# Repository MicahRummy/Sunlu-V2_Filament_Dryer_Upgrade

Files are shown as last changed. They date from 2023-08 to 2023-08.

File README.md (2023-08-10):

# Sunlu-V2_Filament_Dryer_Upgrade
 Upgraded the Sunlu PCB and Firmware.

I had to redesign the cover on the orginal design, and cut a hole for the inductor and aliminum capacitor which didn't fit in the original enclosure. I used the wrong JST connectors, so I had to cut a hole for those as well, but that can be avoided with horizontal connectors instead of vertical. I provided all the design files and Code. The PCB, Schematic, and cover were designed inside Fusion 360. I used a generic OLED display, which I got off of amazon, link below. Most other components can be found in the BOD.csv.

UCTRONICS 0.96 Inch OLED Module... https://www.amazon.com/dp/B072Q2X2LL?ref=ppx_pop_mob_ap_share

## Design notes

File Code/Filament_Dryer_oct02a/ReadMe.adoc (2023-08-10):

:Author: micahrumm
:Email:
:Date: 02/10/2022
:Revision: version#
:License: Public Domain

= Project: {Project}

Describe your project

== Step 1: Installation
Please describe the steps to install this project.

For example:

1. Open this file
2. Edit as you like
3. Release to the World!

== Step 2: Assemble the circuit

Assemble the circuit following the diagram layout.png attached to the sketch

== Step 3: Load the code

Upload the code contained in this sketch on to your board

=== Folder structure

....
 sketch123                => Arduino sketch folder
  âââ sketch123.ino       => main Arduino file
  âââ schematics.png      => (optional) an image of the required schematics
  âââ layout.png          => (optional) an image of the layout
  âââ ReadMe.adoc         => this file
....

=== License
This project is released under a {License} License.

=== Contributing
To contribute to this project please contact: 

=== BOM
Add the bill of the materials you need for this project.

|===
| ID | Part name      | Part number | Quantity
| R1 | 10k Resistor   | 1234-abcd   | 10       
| L1 | Red LED        | 2345-asdf   | 5        
| A1 | Arduino Zero   | ABX00066    | 1        
|===

=== Help
This document is written in the _AsciiDoc_ format, a markup language to describe documents. 
If you need help you can search the http://www.methods.co.nz/asciidoc[AsciiDoc homepage]
or consult the http://powerman.name/doc/asciidoc[AsciiDoc cheatsheet]

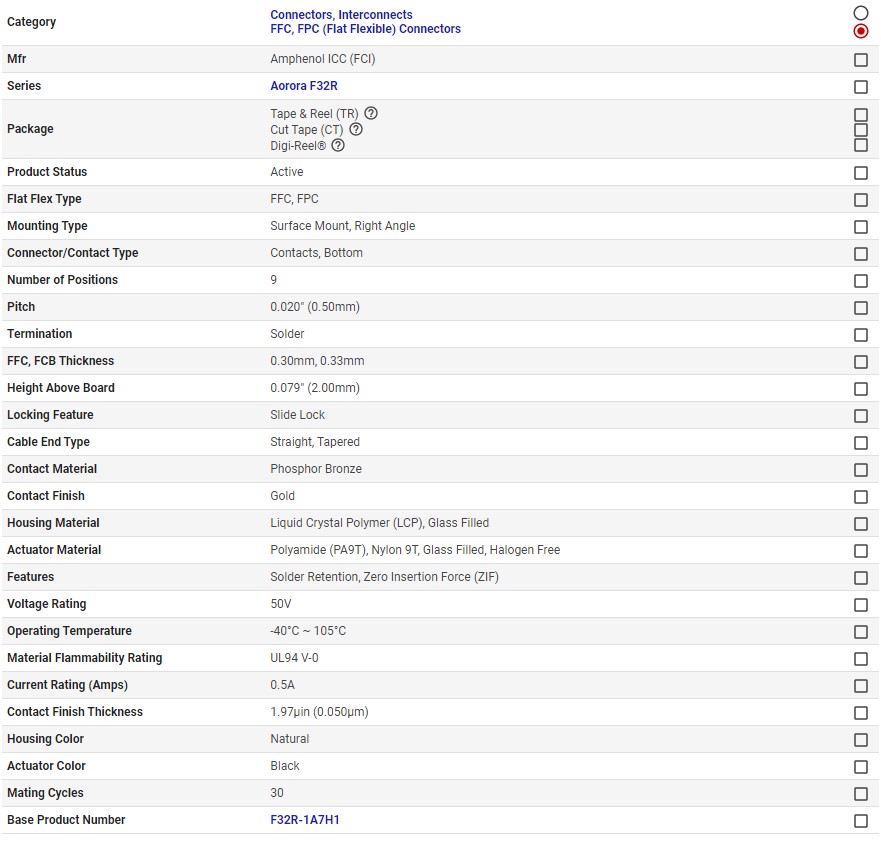
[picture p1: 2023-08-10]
Datasheets/Ribbon Connector Specs_Screenshot 2022-07-01 185358.jpg

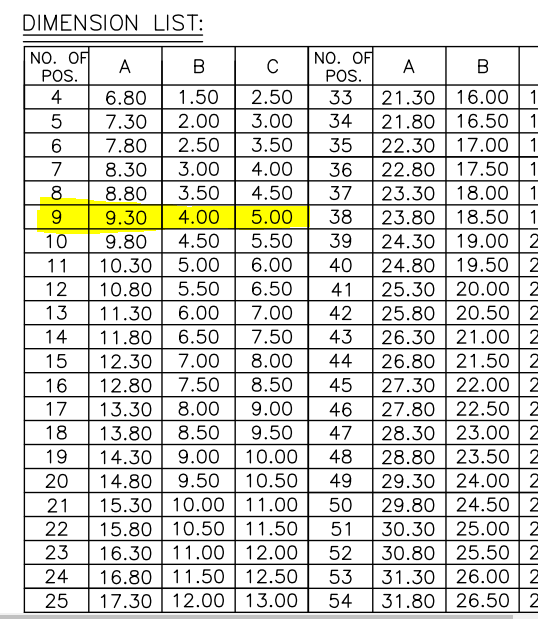
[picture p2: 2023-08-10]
Datasheets/Ribbon Connector.png

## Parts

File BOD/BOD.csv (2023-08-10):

Index | Digi-Key Part # | Manufacturer Part Number | Description | Customer Reference | Quantity | Backorder | Unit Price | Extended Price | Note
1 | 565-4186-1-ND | HHXB350ARA680MF80G | CAP ALUM HYB 68UF 20% 35V SMD |  | 4 | 0 | $1.50 | $6.00
2 | MAX5035BASA+-ND | MAX5035BASA+ | IC REG BUCK 5V 1A 8SOIC |  | 3 | 0 | $5.06 | $15.18
3 | 308-CDRH127L125NP-101MCCT-ND | CDRH127L125NP-101MC | FIXED IND 100UH 2A 171.2MOHM SMD |  | 2 | 0 | $1.40 | $2.80
4 | 3757-SB56AFC_R1_00001CT-ND | SB56AFC_R1_00001 | DIODE SCHOTTKY 60V 5A SMAF-C |  | 4 | 0 | $0.42 | $1.68
5 | 718-1004-1-ND | 594D686X0010C2T | CAP TANT 68UF 20% 10V 2812 |  | 2 | 0 | $3.28 | $6.56
6 | CR0805-FX-1004ELFCT-ND | CR0805-FX-1004ELF | RES SMD 1M OHM 1% 1/8W 0805 |  | 100 | 0 | $0.01 | $1.15
7 | 738-RMCF0805FT383KCT-ND | RMCF0805FT383K | RES 383K OHM 1% 1/8W 0805 |  | 100 | 0 | $0.01 | $1.09
8 | 455-2955-1-ND | BM02B-SRSS-TBT(LF)(SN) | CONN HEADER SMD 2POS 1MM |  | 4 | 0 | $0.64 | $2.56 | Get Horizontal instead of vertical.
9 | 455-2997-ND | A02SR02SR30K51A | JUMPER 02SR-3S - 02SR-3S 2" |  | 2 | 0 | $1.08 | $2.16
10 | WM15692-ND | 797581009 | DURA-CLICK 300MM 26AWG PRE-CRIMP |  | 3 | 0 | $1.33 | $3.99
11 | IRLR2705PBFCT-ND | IRLR2705TRPBF | MOSFET N-CH 55V 28A DPAK | DONT THROW A FET | 10 | 0 | $0.82 | $8.17
12 | 2019-RN73R2ETTD1003B25CT-ND | RN73R2ETTD1003B25 | RESISTOR THIN FILM 1210 SIZE |  | 4 | 0 | $0.80 | $3.20
13 | 1597-113991054-ND | 113991054 | SEEED STUDIO XIAO ESP32C3 WIFI+B |  | 3 | 0 | $4.99 | $14.97
14 | RBR3MM60ATFCT-ND | RBR3MM60ATFTR | DIODE SCHOTTKY 60V 3A PMDU |  | 10 | 0 | $0.32 | $3.17
15 | RMCF0603FT330RCT-ND | RMCF0603FT330R | RES 330 OHM 1% 1/10W 0603 |  | 100 | 0 | $0.01 | $0.61
 |  |  |  |  |  |  | Subtotal | $73.29 | Reuse power connections from old PCB, or find new ones.

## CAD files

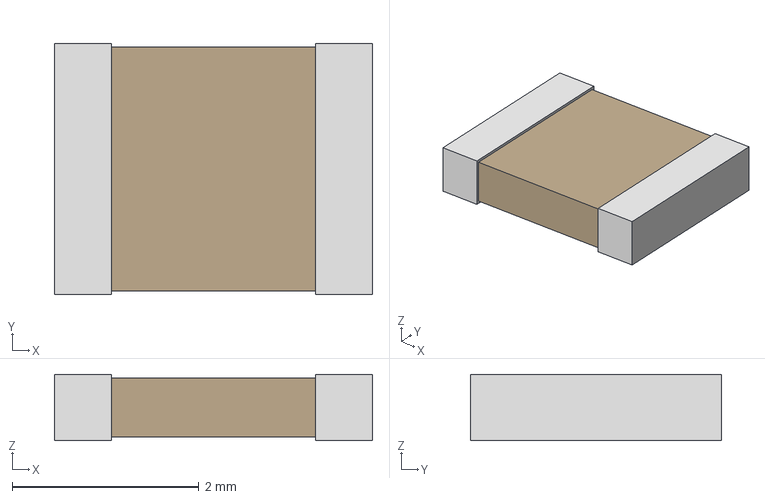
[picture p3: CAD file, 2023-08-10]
Eagle Libraries/100K RESISTOR/ul_RN73R2ETTD1003B25/2022-11-03_19-58-43/STEP/RES_RN73R2E_KOA.step
3.40 x 2.69 x 0.711 mm

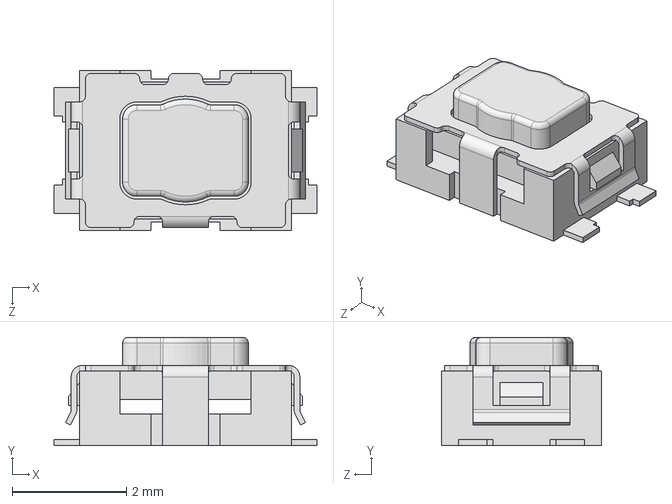
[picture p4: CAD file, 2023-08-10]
Eagle Libraries/Tactile Button/TL6330AF200Q--3DModel-STEP-613395.STEP
4.60 x 1.90 x 2.80 mm

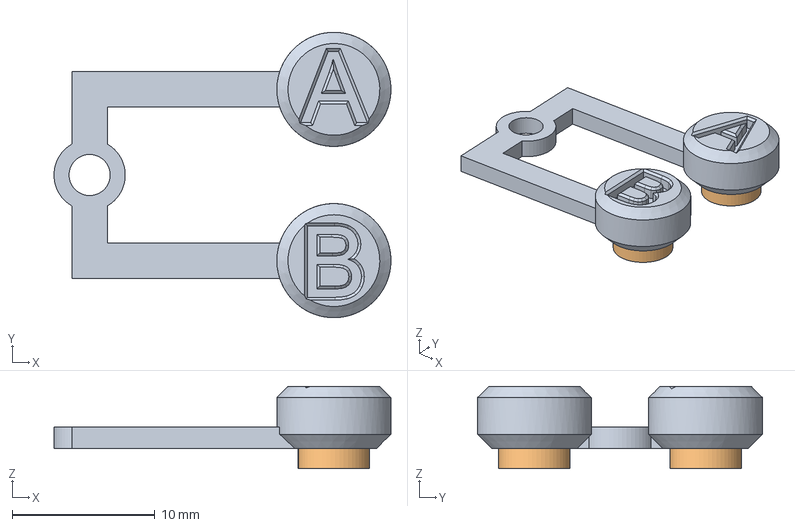
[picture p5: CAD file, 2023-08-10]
Step/Filament Dryer Cover v39.step
23.6 x 20.0 x 5.75 mm

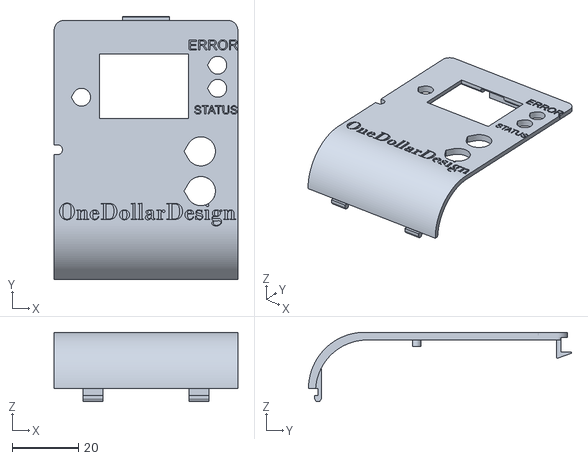
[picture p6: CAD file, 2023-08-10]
stl&3mf/Lid V8.stl
55.5 x 79.5 x 21.0

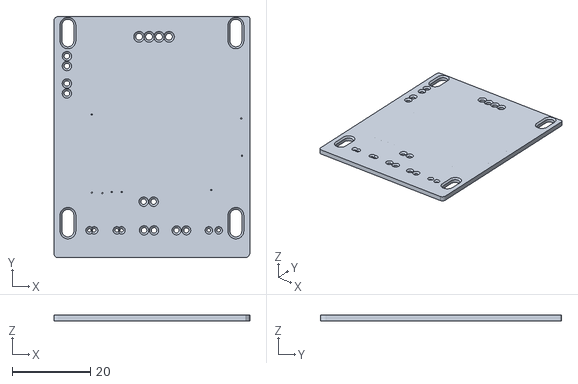
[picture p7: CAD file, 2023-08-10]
stl&3mf/PCB Board 0.2 Tolerance.stl
50.0 x 61.6 x 1.50

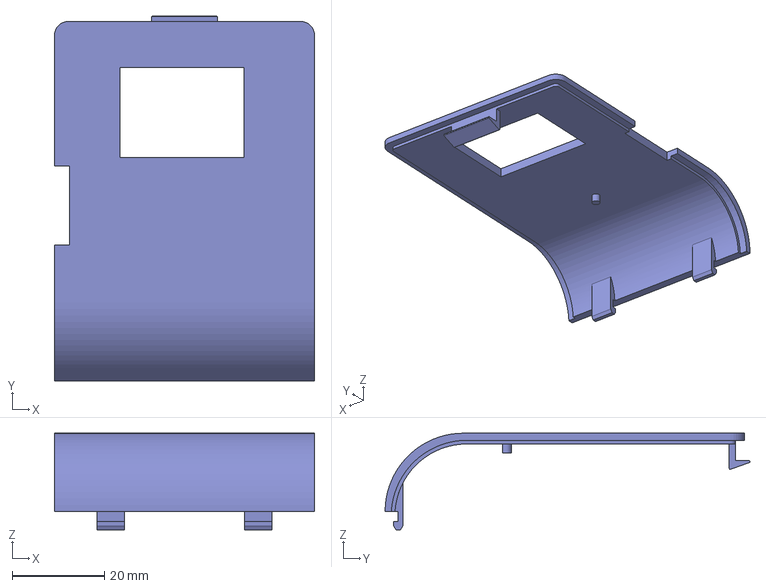
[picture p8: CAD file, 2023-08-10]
stl&3mf/Lid V1.3mf
56.5 x 79.3 x 21.0 mm

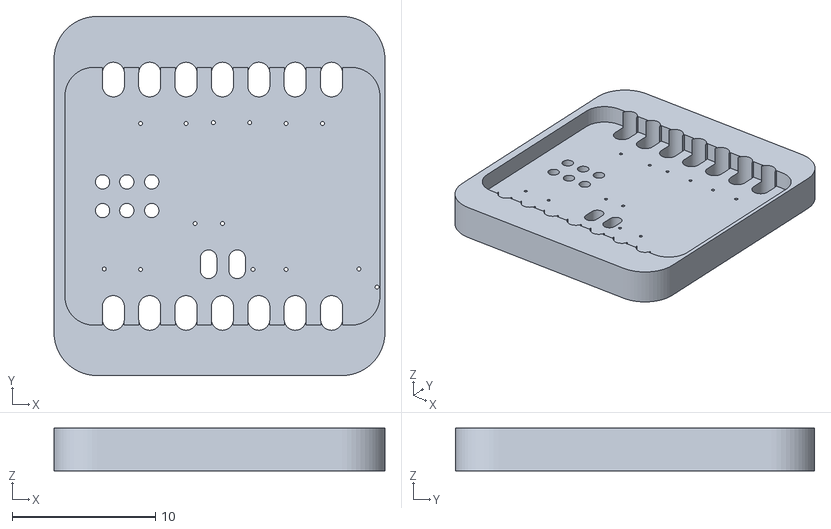
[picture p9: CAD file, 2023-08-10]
stl&3mf/Xiao ESP32 Stencil.stl
23.1 x 25.1 x 3.00

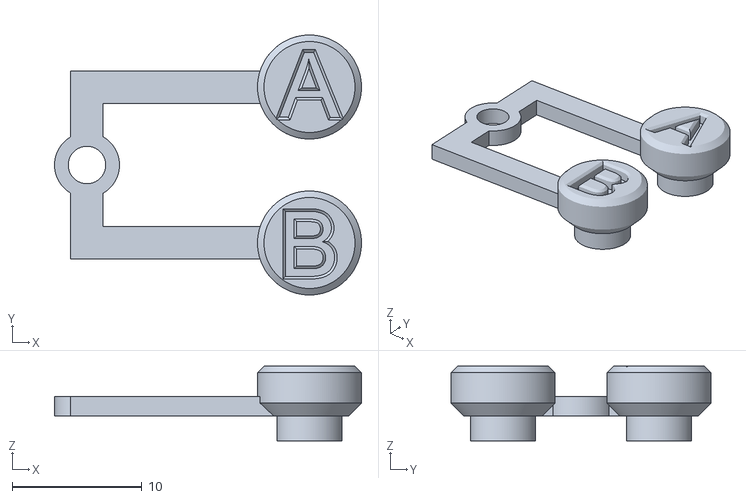
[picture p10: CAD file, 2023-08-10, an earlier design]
stl&3mf/Button Press V4.stl
23.6 x 20.0 x 5.75

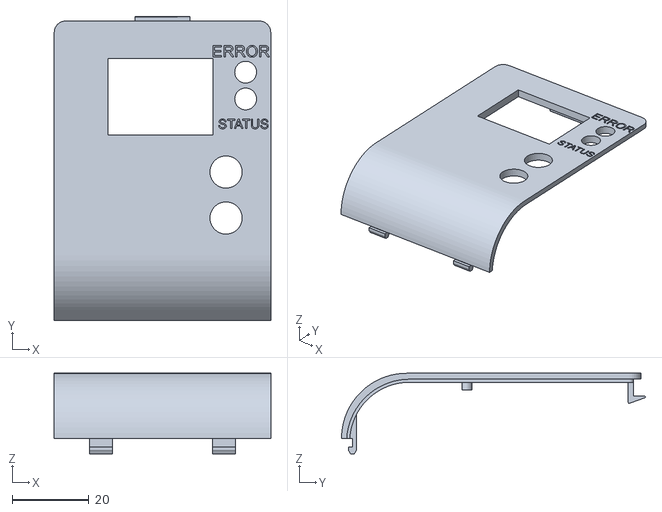
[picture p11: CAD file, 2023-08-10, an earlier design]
stl&3mf/Lid V2.stl
56.5 x 79.3 x 21.0

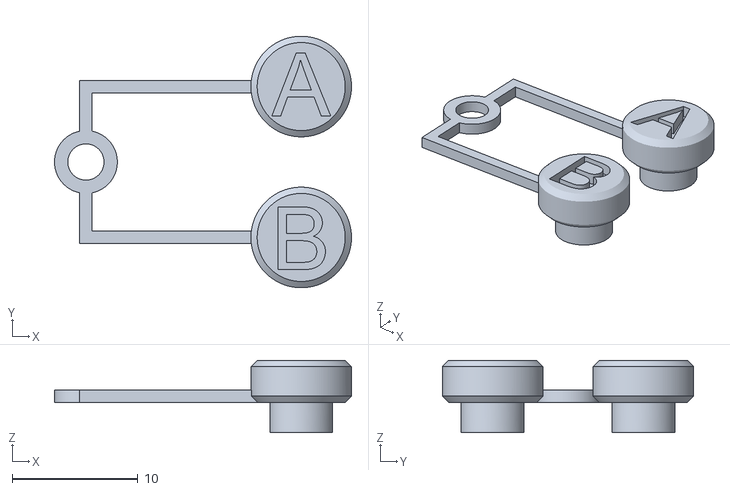
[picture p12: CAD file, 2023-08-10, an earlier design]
stl&3mf/Button Press V3.stl
23.6 x 20.0 x 5.75

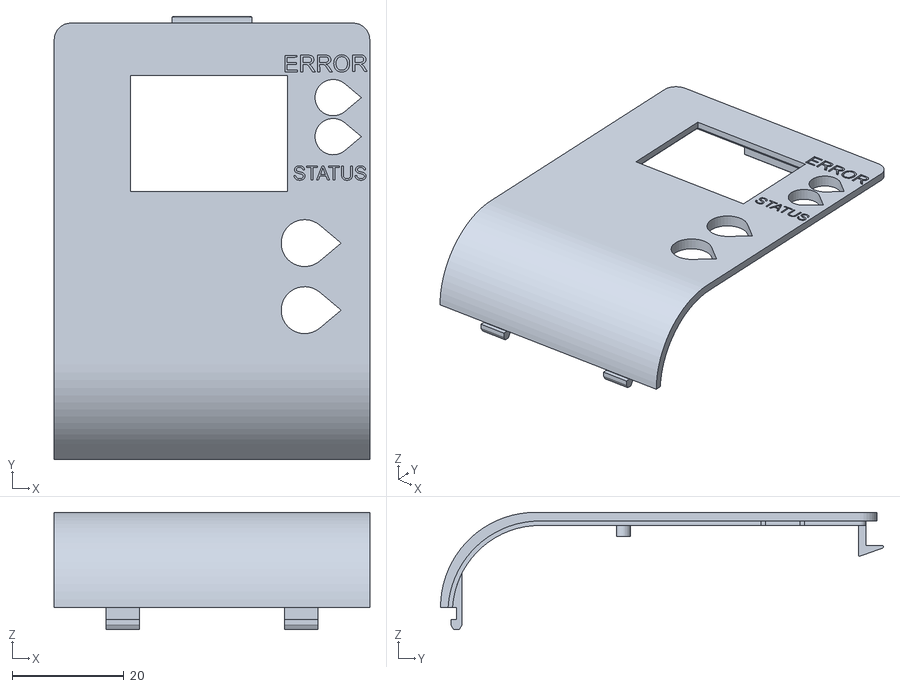
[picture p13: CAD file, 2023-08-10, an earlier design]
stl&3mf/Lid V3.stl
56.5 x 79.3 x 21.0

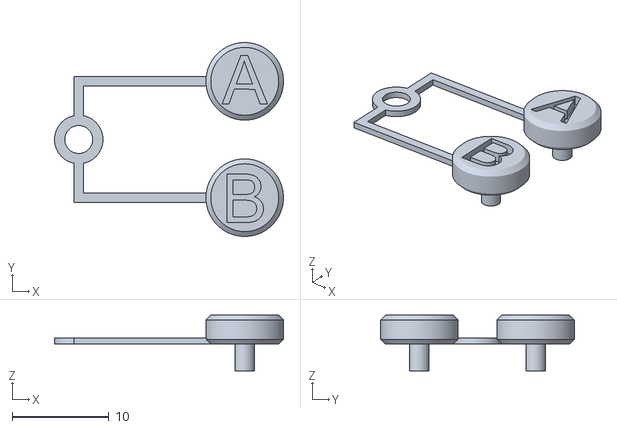
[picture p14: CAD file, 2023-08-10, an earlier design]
stl&3mf/Button Press V2.stl
23.6 x 20.0 x 5.75

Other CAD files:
stl&3mf/PCB Board.stl
stl&3mf/Button Press V5.stl
stl&3mf/Lid V6.stl
stl&3mf/Lid V4.stl
stl&3mf/Lid V7.stl
stl&3mf/Button Press V1.stl
stl&3mf/Lid V5.stl

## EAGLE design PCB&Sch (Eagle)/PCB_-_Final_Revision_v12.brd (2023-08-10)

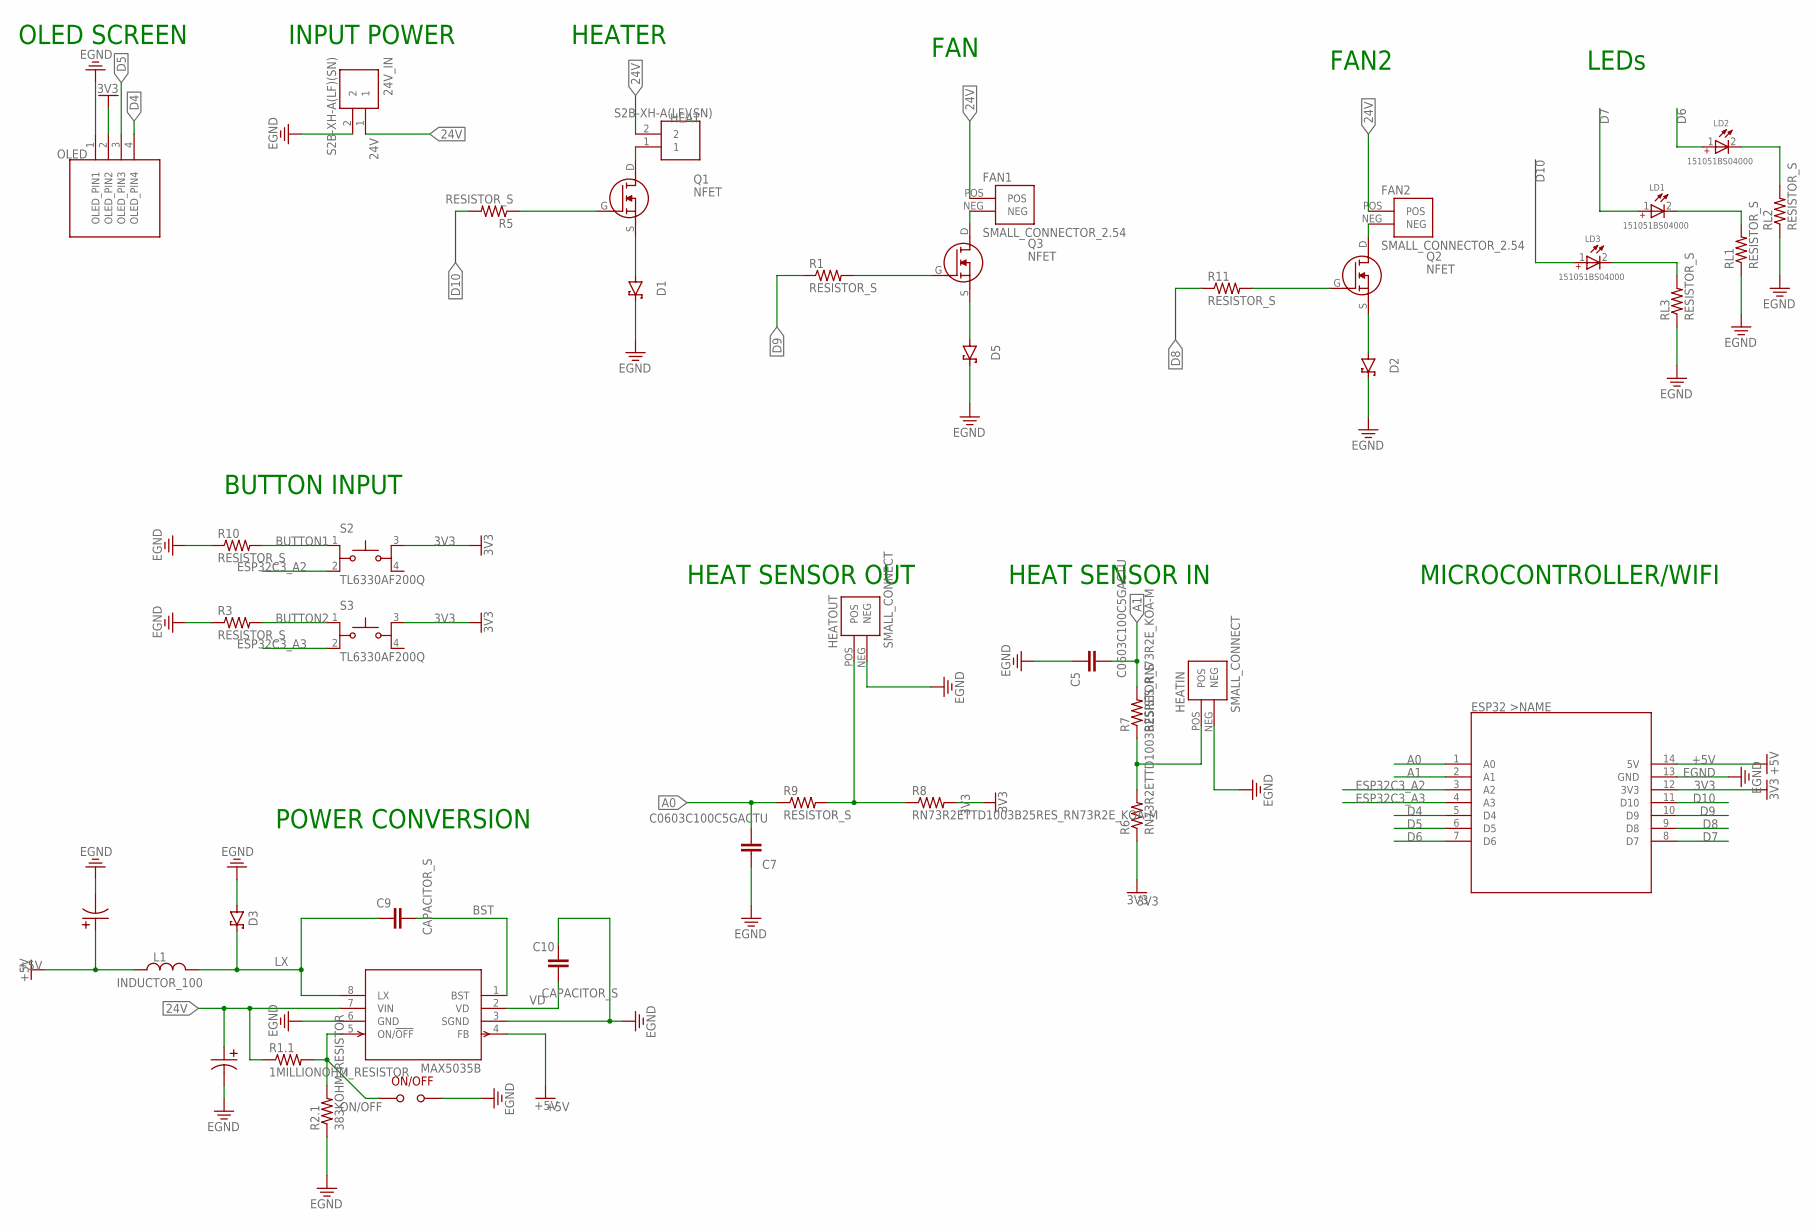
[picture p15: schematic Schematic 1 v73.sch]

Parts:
24V_IN: S2B-XH-A(LF)(SN); HDR-02/RA
C5, C7: C0603C100C5GACTU; CAP_0603
C9, C10: CAPACITOR_S; CAPACITOR_M
D1, D2, D5: ES1D; SCHOTTKY_DIODE_S
D3: MBR0520LT1G; PANJIT_SB52AFC~SB56AFC_SERIES_DIODE
ESP32C3: XIAO_ESP32C3_ALT; XIIO_ESP32C3_ALT
FAN1, FAN2: SMALL_CONNECTOR_2.54; SMALL_CONNECT2.54
HEAT: S2B-XH-A(LF)(SN); HDR-02/RA
HEATIN: SMALL_CONNECT
HEATOUT: SMALL_CONNECT
L1: INDUCTOR_100; 100UH_INDUCTOR
LD1, LD2, LD3: 151051BS04000; WL-TMRC_5MM
OLED: I2C_OLED
ON/OFF: SOLDER_JUMPER
PC1: POLORIZED_100UF; TANTALUM_CAPACITOR_68UF
PC2: 68UF_POLORIZED_CAP; 68UF_CAPAE830X1000N
Q1, Q2, Q3: NFET
R1, R3, R5, R7, R9, R10, R11: RESISTOR_S
R1.1: 1MILLIONOHM_RESISTOR; 1MOHM_RESISTOR_SMD
R2.1: 383KOHM_RESISTOR; 383KOHM_RESISTOR_0805
R6, R8: RN73R2ETTD1003B25RES_RN73R2E_KOA-M; RES_RN73R2E_KOA-M
RL1, RL2, RL3: RESISTOR_S
S2, S3: TL6330AF200Q; SW_TL6330AF200Q
U1: MAX5035BASA+T; 21-0041B_8_MXM-M

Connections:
3V3: ESP32C3.12 (3V3), OLED.2 (OLED_PIN2), R6.2, R8.1, S2.3, S3.3
24V: 24V_IN.1, FAN1.POS, FAN2.POS, HEAT.2, PC2.POS, R1.1.2, U1.7 (VIN)
+5V: ESP32C3.14 (5V), L1.P$1 (1), PC1.+ (POS), U1.4 (FB)
A0: C7.2, ESP32C3.1 (A0), R9.2
A1: C5.2, ESP32C3.2 (A1), R7.1
BST: C9.2, U1.1 (BST)
BUTTON1: R10.1, S2.1
BUTTON2: R3.1, S3.1
D4: ESP32C3.5 (D4), OLED.4 (OLED_PIN4)
D5: ESP32C3.6 (D5), OLED.3 (OLED_PIN3)
D6: ESP32C3.7 (D6), LD2.1 (+)
D7: ESP32C3.8 (D7), LD1.1 (+)
D8: ESP32C3.9 (D8), R11.2
D9: ESP32C3.10 (D9), R1.2
D10: ESP32C3.11 (D10), LD3.1 (+), R5.1
DRAIN1: HEAT.1, Q1.D
DRAIN2: FAN1.NEG, Q3.D
DRAIN3: FAN2.NEG, Q2.D
EGND: 24V_IN.2, C5.1, C7.1, C10.1, D1.NEG, D2.NEG, D3.POS, D5.NEG, ESP32C3.13 (GND), HEATIN.NEG, HEATOUT.NEG, OLED.1 (OLED_PIN1), ON/OFF.P$2, PC1.- (NEG), PC2.NEG, R2.1.2, R3.2, R10.2, RL1.2, RL2.2, RL3.2, U1.3 (SGND), U1.6 (GND)
ESP32C3_A2: ESP32C3.3 (A2), S2.2
ESP32C3_A3: ESP32C3.4 (A3), S3.2
GATE1: Q1.G, R5.2
GATE2: Q3.G, R1.1
GATE3: Q2.G, R11.1
HEAT_IN: HEATIN.POS, R6.1, R7.2
HEAT_OUT: HEATOUT.POS, R8.2, R9.1
LX: C9.1, D3.NEG, L1.P$2 (2), U1.8 (LX)
ON/OFF: ON/OFF.P$1, R1.1.1, R2.1.1, U1.5 (ON/!OFF)
RL1: LD1.2 (-), RL1.1
RL2: LD2.2 (-), RL2.1
RL3: LD3.2 (-), RL3.1
SOURCE1: D1.POS, Q1.S
SOURCE2: D5.POS, Q3.S
SOURCE3: D2.POS, Q2.S
VD: C10.2, U1.2 (VD)

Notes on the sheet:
POWER CONVERSION
INPUT POWER
OLED SCREEN
HEAT SENSOR IN
HEAT SENSOR OUT
HEATER
FAN
MICROCONTROLLER/WIFI
BUTTON INPUT
FAN2
LEDs

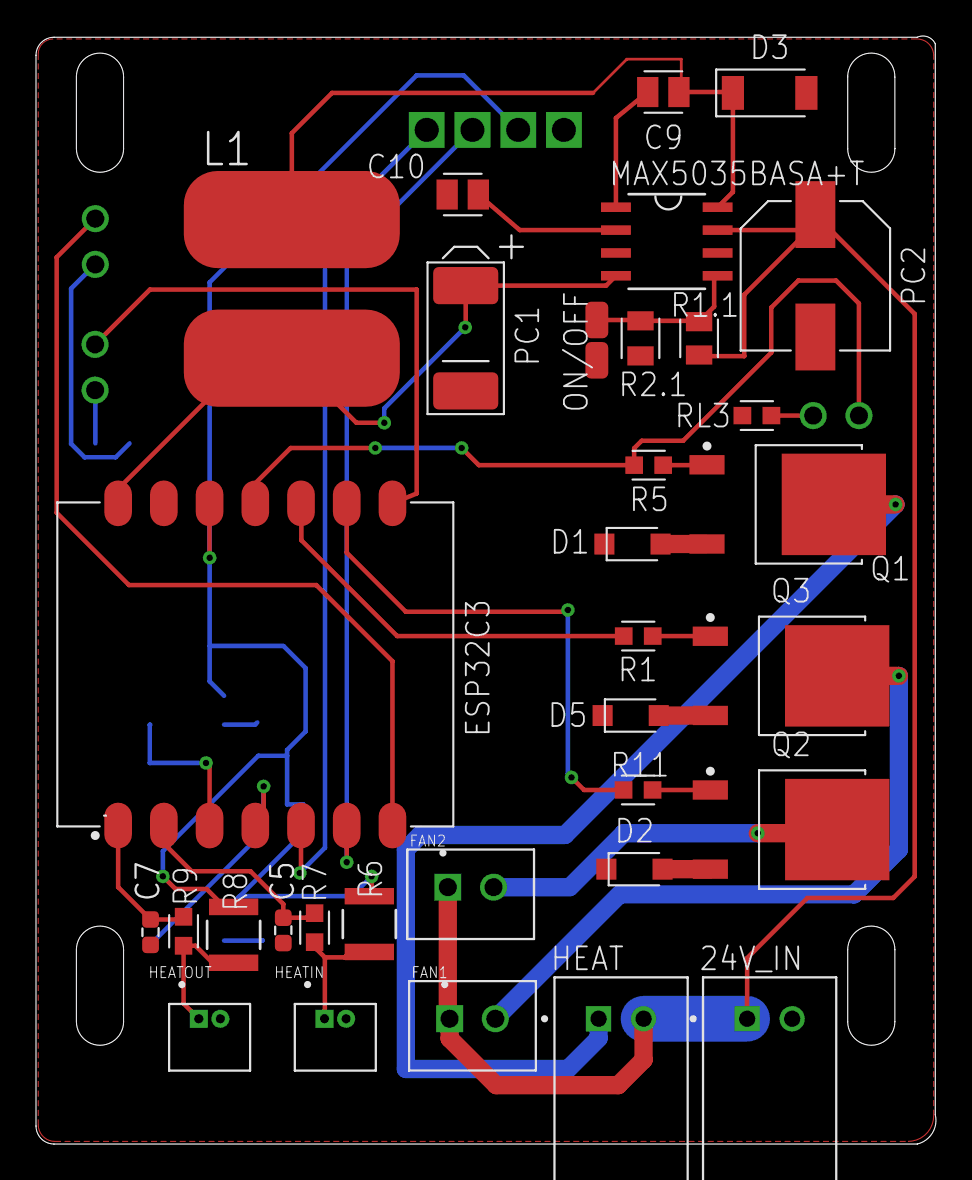
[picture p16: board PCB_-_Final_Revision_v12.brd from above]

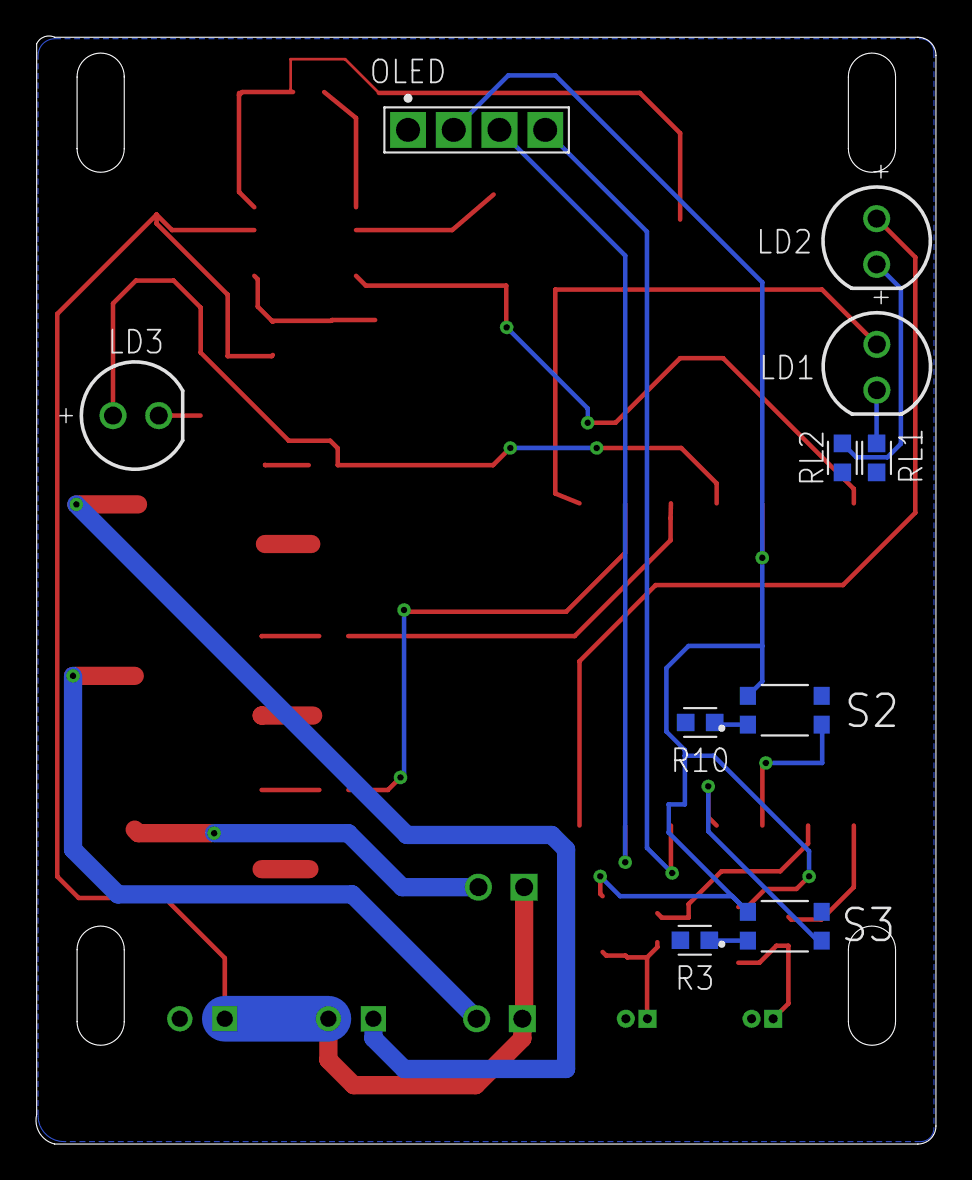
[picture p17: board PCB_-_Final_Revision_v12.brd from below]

Board: 2 copper layers, 50.0 x 61.6 mm, 43 parts (10 on the bottom side), 35 nets.

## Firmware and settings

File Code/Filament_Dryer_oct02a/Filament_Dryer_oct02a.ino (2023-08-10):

#include "Button.h"
#include "arduino_secrets.h"
#include "thingProperties.h"
//Hidden Variables:
  //    String message;
  //   int cTemperature;
  //   int setTime;
  //   int tempatureSet;
  //   CloudTime timeLeft;

#include "DryingFunctions.h"
#include "Temperature.h"
#include "Fan.h"

//buttons
  //10s reset function:
  void reset(){
    ESP.restart();
  }

  Button button1(4, reset, 3);
  Button button2(5, reset, 3);

  Fan fan1(9);
  Fan fan2(8);

//thermistors:
  Temperature dummy;
  Temperature sensorout(0, 3950, 100000, 298.15, heatOutPin);
  Temperature sensorin(sizeof(sensorout)+sensorout.getAddress(), 3950, 100000, 298.15, heatInPin);

void setup() {
  // Initialize serial and wait for port to open:
  Serial.begin(baudrate); 

  //initialize eeprom
  EEPROM.begin(512);

  // Output pins
  pinMode(heatPin, OUTPUT);
  pinMode(statusLed, OUTPUT);
  pinMode(errorLed, OUTPUT);
  // input pins
  // pinMode(heatInPin, INPUT);
  // pinMode(heatOutPin, INPUT);

  // ensure that heat and fan are off at start.
  analogWrite(heatPin, 0);

  // start Runtime variable
  runTime = millis();

  //set up OLED Startup Screen
  // SSD1306_SWITCHCAPVCC = generate display voltage from 3.3V internally
  if(!display.begin(SSD1306_SWITCHCAPVCC, SCREEN_ADDRESS)) {
    displayError("SSD1306 allocation failed");
    for(;;); // Don't proceed, loop forever
  }

  // Clear the buffer.
  display.clearDisplay();
  display.setTextSize(1);
  display.setTextColor(WHITE);
  display.setCursor(10,0);
  display.println("Lets heat filament!");
  display.display();
  
  //statusLed blink for 1 second
  for (int i =0; i < 10; i++){
    digitalWrite(statusLed, HIGH);
    delay(100);
    digitalWrite(statusLed, LOW);
    delay(100);
  }

  //get last saved in EEPROM:
  displayError("getting from memory:\n");

//sensor in:
  display.println("Inside Sensor:");
  EEPROM.get(sensorin.getAddress(), dummy);

  if (!dummy.printb() || isnan(dummy.printb())){
    EEPROM.put(sensorin.getAddress(), sensorin);
    display.print("Success put! ");
    display.println(dummy.printb());
  }
  else{
    EEPROM.get(sensorin.getAddress(), sensorin);
    display.print("Success get!  ");
    display.println(sensorin.printb());
  }

//sensor out:
  display.println("outside sensor:");
  EEPROM.get(sensorout.getAddress(), dummy);

  if (!dummy.printb() || isnan(dummy.printb())){
    EEPROM.put(sensorout.getAddress(), sensorout);
    display.print("Success put!  ");
    display.println(dummy.printb()); 
  }
  else{
    EEPROM.get(sensorout.getAddress(), sensorout);
    display.print("Success get!  ");
    display.println(sensorout.printb());
  }
//commit, start booting.
  EEPROM.commit();
  display.display();
  delay(10000);

  
  // Defined in thingProperties.h
  initProperties();

  // Connect to Arduino IoT Cloud
  ArduinoCloud.begin(ArduinoIoTPreferredConnection);
  /*
     The following function allows you to obtain more information
     related to the state of network and IoT Cloud connection and errors
     the higher number the more granular information youâll get.
     The default is 0 (only errors).
     Maximum is 4
 */
  setDebugMessageLevel(2);
  ArduinoCloud.printDebugInfo();
  display.clearDisplay();
  display.display();
  message = "Ready.";
}

void loop() {
  //get current run time
    runTime = millis();

  //check for heat sensors
    heatOutDetected = checkHeatPin(heatOutPin);
    heatInDetected = checkHeatPin(heatInPin);

  //blink LED
    // blink(statusLed, blinkRate, statusLedBlinkTime);//statusLed not working
    blink(errorLed, errorBlinkRate, errorLedBlinkTime);

  if (!test_mode){//test mode bypasses error handling.

    //if sensors dont exit, terminate code, shut off heat
      checkSensors();

    // if an error occured, dont proceed.
      if (generalError){
        return;
      }
  }

    //code below runs if no error occured.

  //get updates
    updateCloud();

  //time setting
    if (wait_answer_time){
        disable_chat = true;
        while (message == "How many hours?" || (millis() - message_event) > 20000){//20 second timeout
          ArduinoCloud.update();
        }
        wait_answer_time = false;
        if (message.toInt() > 0){
          countDown = message.toInt() * 3600000;// in millis
          timeLeft = countDown / 3600000 ;//in hours
          countDownTriggered = true;
          message = "time set.";
          ArduinoCloud.update();
          countDownEvent = millis();
        }
        else if (millis() - message_event > 20000){
          message = "Timeout occured.";
        }
        else if (message == "0"){
          countDown = 0;
          timeLeft = countDown;
          countDownTriggered = false;
          message = "time removed.";
          ArduinoCloud.update();
        }
        else{
          message = "Invalid Time.";
        }
      }

  //Limit Setting
    if (wait_answer_limit){
        disable_chat = true;
        while (message == "New Plate Max temp?" || (millis() - message_event) > 20000){//20 second timeout
          ArduinoCloud.update();
        }
        wait_answer_limit = false;
        if (message.toInt() > 60){
          plate_limit = message.toInt();
          message = "Limit set to " + message + ".";
        }
        else if (millis() - message_event > 20000){
          message = "Timeout occured.";
        }
        else{
          message = "Invalid input.";
        }
      }

  //Speed Setting
    if (wait_answer_speed){
        disable_chat = true;
        while (message == "New Fan speed?" || (millis() - message_event) > 20000){//20 second timeout
          ArduinoCloud.update();
        }
        wait_answer_speed = false;
        if (message.toInt() > 0){
          fan1.fan_speed = map(message.toInt(), 0, 100, 0, 255);
          fan2.fan_speed = map(message.toInt(), 0, 100, 0, 255);
          fan1.fanPWM();
          fan2.fanPWM();
          fan_override = true;
          message = "Fan Override on. Fan at " + message + "%.";
        }
        else if (millis() - message_event > 20000){
          message = "Timeout occured.";
        }
        else{
          message = "Invalid input.";
        }
      }

  //calibration
    if (calibration){
      thermistor = requestThermistor();//get which thermistor.
      delay(3000);
      //interpret reading
        //if cancel code sent
        if (thermistor < 0){
          message = "Cancled.";
          displayError(message);
          delay(10000);
          ArduinoCloud.update();
          calibration = false;//reset calibration
          return;
        }
        else if (thermistor == 1){
          dummy = sensorout;
        }
        else if (thermistor == 2){
          dummy = sensorin;
        }
        //if input is not as expected:
        else{
          displayError("Invalid input.");
          message = "Invalid input.";
          ArduinoCloud.update();
          calibration = false;//reset calibration
          return;
        }

      realtemp = requestRealTemp();
      dummy.calibrate(realtemp);//changes b value
      EEPROM.put(dummy.getAddress(), dummy);//saves the object
      EEPROM.commit();
      rewriteLine1(8, "New B value = ");
      display.println(String(dummy.printb()));
      display.println("Resistance: = ");
      display.println(String(dummy.getResistance()));
      display.display();
      delay(10000);
      getAllThermistors();//retrieves new values to propper variables
      rewriteLine1(56, "Ready.");
      calibration = false;//reset calibration
    }
    
  //read temperature:
    heatTempOut = sensorout.getTemp(sensorout.getResistance());
    heatTempIn = sensorin.getTemp(sensorin.getResistance());
    // heatTemp = (heatTempOut + heatTempIn) / 2;//rounded temperature - averaged
    heatTemp = heatTempOut;//to get an integer instead of a float
    cTemperature = heatTemp;//to read temp on arduino cloud dashboard

  //constantly update temperature
    clearLine(18, 2);
    display.setTextSize(2);
    display.setCursor(30,20);
    // y = round(heatTemp);
    // display.print(y);
    display.print(heatTemp);
    display.print("C");
    display.display();
    

  //cooldown
    if (!heating){
      if (!fan_override){      
          if (heatTempIn >= 50){
            fan1.fanOn();
            fan2.fanOn();
          }
          else{
            fan1.fanOff();
            fan2.fanOff();
          }
        }

      coolDown();
      button2.attach(switchMaterial);
    }
  //heat filament
    else{
      //Fan speeds
        if (!fan_override){      
          diff = (heatTempIn-heatTempOut);
          if (diff > 5 || overflowWarning){//if the difference between thermistors is too great
            fan1.fanOn();
            fan2.fanOn();
          }
          else if (diff < 1){
            fan1.fanOff();
            fan2.fanOff();
          }
          else{
            fan1.fan_speed = map(diff, 0, 5, 0, 255);
            fan2.fan_speed = map(diff, 0, 5, 0, 255);
            fan1.fanPWM();
            fan2.fanPWM();
          }
        }

      //status event
      if ((millis() - status_event) > 60000){//update status every minute{
        status_event = millis();
        sendStatus();
      }

      //heat function & buttons
      heatFilament();
      button1.attach(coolDown);
      button2.detach(0);
    }

  //count down timer triggered, with heating
    if (countDownTriggered && heating){
      if ((millis() - countDownEvent) >= 6000){//after every minute
        countDown = countDown - (millis() - countDownEvent);//subtract time lasped...
        countDownEvent = millis();
        clearLine(45, 1);
        display.setCursor(0, 45);
        display.setTextSize(1);
        display.print("Time left: ");
        display.print(String(countDown / 60000 + "m"));
        display.display();
        timeLeft = countDown / 60000;//in minutes
        ArduinoCloud.update();//push change
      }

      if (countDown <= 0){
        countDownTriggered = false;//turns off countdown
        coolDown();// turns off heating
        clearLine(45, 1);
        display.setCursor(0, 45);
        display.setTextSize(1);
        display.print("Heating Turned off due to timeout...");
        display.display();
        timeLeft = 0;
        message = "Heating Turned off due to timeout...";
        ArduinoCloud.update();//push change
        delay(3000);
      }
    }

    
  //calls the function associated to a button:
    button1.call();
    button2.call();
    } //end main loop
    
//function to reset thermistors by memory.
  void getAllThermistors(){
    displayError("New values:");
    EEPROM.get(sensorin.getAddress(), sensorin);
    EEPROM.get(sensorout.getAddress(), sensorout);

    display.println();
    display.println("inside");
    display.print("b: ");
    display.println(sensorin.printb());
    display.print("res: ");
    display.println(sensorin.getResistance());
    display.println("outside");
    display.print("b: ");
    display.println(sensorout.printb());
    display.print("res: ");
    display.println(sensorout.getResistance());
    display.display();
    delay(5000);
  }

//Button functions:
  bool menuExit;
  int selection;
  int choice_count_up;
  int choice_count_down;

//button 1 functions:
  void pla(){
    rewriteLine1(0, "Set to 50C");  
    tempatureSet = 50;
    onTempatureSetChange();
    message = "heating to 50C.";
  }
  void tpu(){
    rewriteLine1(0, "Set to 55C");  
    tempatureSet = 55;
    onTempatureSetChange();
    message = "heating to 55C.";
  }
  void petg(){
    rewriteLine1(0, "Set to 60C");  
    tempatureSet = 60;
    onTempatureSetChange();
    message = "heating to 60C.";
  }
  void downButton(){
    selection --;
    if (selection < 0){
      selection = 0;
    }
  }

  //heat menu, sets temperature.
    void heatMenu(){
      displayError("Set heat.");
      rewriteLine1(56, message);
      rewriteLine1(8, "Temperature:");
      menuExit = false;
      selection = 50;
      choice_count_up = 75;//75 celcius limit.
      choice_count_down = 0;//0 is off...
      button2.attach(upButton);
      button1.attach(downButton);
      button1.attach(goBack, 4);
      button2.attach(goBack, 4);
      button1.attach(downButton);
      button2.attach(selecter, 1);//sets select to long press.
      button1.attach(selecter, 1);//sets select to long press.
      //menu loop:
      while (!menuExit){
        button1.call();
        button2.call();

        clearLine(18, 2);
        display.setTextSize(2);
        display.setCursor(40,20);
        display.print(selection);
        display.print("C");
        display.display();
      }
      //finish with selection as temperature.
      tempatureSet = selection;
      onTempatureSetChange();
      message = "heating to " + String(selection) + ".";
      button1.detach(0);//detaches button down.
      button1.detach(1);//detaches selecter.
      button2.detach(0);//detaches button up.
      button2.detach(1);//detaches selecter.
      button2.detach(4);//detaches goBack.
      button1.detach(4);//detaches goBack.
      if (selection == 0){
        return;
      }
      displayError("Heat Set to: ");
      display.print(selection);
      display.display();
      delay(3000);
    }

  //time menu. takes a full screen, is a loop. sets the heat time limit.
    void timeMenu(){
      displayError("Set timout.");
      rewriteLine1(56, message);
      rewriteLine1(8, "time:");
      menuExit = false;
      selection = 0;
      choice_count_up = 72;//72 hour limit.
      choice_count_down = 0;
      button2.attach(upButton);
      button1.attach(downButton);
      button2.attach(selecter, 1);//sets select to long press.
      button1.attach(selecter, 1);//sets select to long press.
      button2.attach(goBack, 4);//sets select to long press.
      button1.attach(goBack, 4);//sets select to long press.
      //menu loop:
      while (!menuExit){
        button1.call();
        button2.call();

        clearLine(18, 2);
        display.setTextSize(2);
        display.setCursor(40,20);
        display.print(selection);
        display.print("H");
        display.display();
      }
      //finish with selection as time.
      setTime = selection;
      onSetTimeChange();
      button1.detach(0);//detaches button down.
      button1.detach(1);//detaches selecter.
      button2.detach(0);//detaches button up.
      button2.detach(1);//detaches selecter.
      button1.detach(4);//detaches goBack.
      button2.detach(4);//detaches goBack.
      if (selection == 0){
        return;
      }
      displayError("Time Set to: ");
      display.print(selection);
      display.display();
      delay(3000);
    }

//button 2 functions:
  //sub menu... displayed at base of screen at all times.
    void switchMaterial(){
      int listlength = 4;

      material++;
      if (material > listlength){
        material = 0;//reset list
      }
      if (material == 0){
        button1.attach(pla);
        message = "set to PLA";
        rewriteLine1(56, message);    
      }
      else if (material == 1){
        button1.attach(tpu);
        message = "set to TPU";
        rewriteLine1(56, message);    
      }
      else if (material == 2){
        button1.attach(petg);
        message = "set to PETG";
        rewriteLine1(56, message);    
      }
      else if (material == 3){
        button1.attach(timeMenu);
        message = "Set timout.";
        rewriteLine1(56, message);    
      }
      else if (material == 4){
        button1.attach(heatMenu);
        message = "Set custom temp.";
        rewriteLine1(56, message);    
      }
    }
  void upButton(){
    selection ++;
    if (selection > choice_count_up){
      selection = choice_count_up;
    }
  }

//dual button commands:
  void selecter(){
    menuExit = true;
  }
  void goBack(){
    menuExit = true;
    selection = 0;
  }
  //end button commands

  int fanStatus (Fan fan){
    if (fan.fanPWMStatus()){
      return map(fan.fan_speed, 0, 255, 0, 100);
    }
    else{
      return fan.fanStatus();
    }
  }

//Status sender
  void sendStatus(){
    message = "Outside Temp:\t" + String(heatTempOut, 1) + "\nInside Temp:\t" + String(heatTempIn, 1) +
              "\nFan value:\t" + String(fanStatus(fan1)) + 
              "\nHeating:\t" + String(heating);
    ArduinoCloud.update();
  }

//When Command gets sent
  void onMessageChange(){
    if (message == "PLA"){
      message = "Heating to 55C...";
      tempatureSet = 55;
      onTempatureSetChange();
    }
    else if (message == "PETG"){
      message = "Heating to 60C...";
      tempatureSet = 60;
      onTempatureSetChange();
    }
    else if (message == "TPU"){
      message = "Heating to 55C...";
      tempatureSet = 55;
      onTempatureSetChange();
    }
    else if (message == "OFF" || (message == "0" && !calibration && !disable_chat) || message == "Off"){
      message = "Heating Off...";
      tempatureSet = 0;
      onTempatureSetChange();
    }
    else if (message == "Calibrate"){
      calibration = true;
      message = "ok...";
      ArduinoCloud.update();
      message = "Calibrating.";
    }
    else if (message == "Clear"){
      if (confirm()){
        clearEEPROM();      
      }
      else {
        message = "Canceled.";
        ArduinoCloud.update();
      }
    }
    else if (message == "Reset"){
      if (confirm()){
        ESP.restart();      
      }
      else{
        message = "Canceled.";
        ArduinoCloud.update();
      }
    }
    else if (message.toInt() > 0 && !calibration && !disable_chat){//any integer
      tempatureSet = message.toInt();
      message = "Heating to " + message + "...";    
      onTempatureSetChange();
    } 
    else if (message == "Fan"){
      if (!fan1.fanStatus() || !fan2.fanStatus()){
        fan1.fanOn();
        fan2.fanOn();

        message = "Fan On.\nFan Override turned on.";
        fan_override = true;
        ArduinoCloud.update();
      }
      else{
        fan1.fanOff();
        fan2.fanOff();

        message = "Fan Off.\nFan Override turned on.";
        fan_override = true;
        ArduinoCloud.update();
      }
    }
    else if (message == "DisableFanOverride" || message == "disablefanoverride" || message == "Disablefanoverride"){
        fan_override = false;
        message = "Fan Override turned off.";
        ArduinoCloud.update();
    }
    else if (message == "Status"){
        sendStatus();
    }
    else if(message == "Test"){
      if (!test_mode){
        test_mode = true;
        message = "test mode on.";
        ArduinoCloud.update();
      }
      else{
        test_mode = false;
        message = "test mode off.";
        ArduinoCloud.update();
      }
    }
    else if (message == "Time"){
      message = "How many hours?";
      message_event = millis();
      wait_answer_time = true;
      ArduinoCloud.update();
    }
    else if (message == "Limit"){
      message = "New Plate Max temp?";
      message_event = millis();
      wait_answer_limit = true;
      ArduinoCloud.update();
    }
    else if (message == "Timeleft"){
      message = String(countDown / 60000) + " minutes.";
      ArduinoCloud.update();
    }
    else if (message == "Fanspeed"){
      message = "New Fan speed?";
      message_event = millis();
      wait_answer_speed = true;
      ArduinoCloud.update();
    }
    else if (message == "!help" || message == "Help" || message == "help"){
      message = "command list:\nReset\nCalibrate\nClear: \tclears eeprom\nOff\nTPU\nPETG\nPLA\nFan\nDisableFanOverride\nStatus\nTest\nTime\nLimit\nTimeleft\nFanspeed";
      ArduinoCloud.update();
    }
    else if (!calibration && !disable_chat){//invalid command
      message = "invalid command.\nType \"help\" for command list.";
      ArduinoCloud.update();
    }
    else{//turn off diable_chat
      disable_chat = false;
    }
    rewriteLine1(56, message);
    ArduinoCloud.update();
  }

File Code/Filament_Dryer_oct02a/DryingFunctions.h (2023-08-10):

#pragma once

#include <Wire.h>
#include <Adafruit_GFX.h>
#include <Adafruit_SSD1306.h>
#include "EEPROM.h"

#ifndef DryingFunctions.h
#define DryingFunctions.h
#endif

#define SCREEN_WIDTH 128 // display display width, in pixels
#define SCREEN_HEIGHT 64 // display display height, in pixels

#define display_RESET -1 // Reset pin # (or -1 if sharing Arduino reset pin)
#define SCREEN_ADDRESS 0x3C ///< See datasheet for Address; 0x3D for 128x64, 0x3C for 128x32

Adafruit_SSD1306 display(SCREEN_WIDTH, SCREEN_HEIGHT, &Wire, display_RESET);

//display functions:
void clearLine(int x, int multiplier){
  int s = x + (8 * multiplier);  
  for (x; x<s; x++){
    for (int y = 0; y<127; y++){
      display.drawPixel(y,x,BLACK);
    }
  }
}

void displayError(String msg){
  clearLine(0, 8);//leaves the last line available.
  display.setTextSize(1);
  display.setTextColor(WHITE);
  display.setCursor(0,0);
  display.print(msg);
  display.display();
}

void rewriteLine1(int x, String str){
    clearLine(x, 1);
    display.setCursor(0, x);
    display.setTextSize(1);
    display.print(str);
    display.display();
}

//Pin Definition Variables
  //24V pins
const int heatPin = 10;//D10 on Board
  //buttons
// const int button1Pin = 4;//D2 on Board
// const int button2Pin = 5;//D3 on Board
  //sensors
const int heatInPin = 3;//D1/A1 on Board
const int heatOutPin = 2;//D0/A0 on Board
  //Indicators
const int statusLed = 20;//D7 on Board
const int errorLed = 21;//D8 on Board

//serial Variables
const int baudrate = 9600;

//Events
int statusLedBlinkTime = 0;
int blinkRate = 0;

int errorLedBlinkTime = 0;
int errorBlinkRate = 0;

int countDown = 0;
int countDownEvent = 0;

int updateEvent = 0;
int updateTiming = 0;

int calibrateevent = 0;

int message_event = 0;

int status_event = 0;

//Values Variables
int material;
int runTime;
float heatTempOut = 0; //current temperature
float heatTempIn = 0; //current temperature
int heatTemp = 0; //average temp
int y;
int heatIncrement = 0;
int overflow = 5;
int sensorThreshold = 30;
int diff;
float realtemp;
int plate_limit = 95;

//Bools Variables
bool heatInDetected = false;
bool heatOutDetected = false;
bool heating = false;
bool countDownTriggered = false;
bool overflowWarning = false;
bool heatInError = false;
bool heatOutError = false;
bool generalError = false;
bool awaitUpdate = true;
bool calibration = false;
bool stable = false;
bool fan_override = false;
bool test_mode = false;
bool wait_answer_time = false;
bool wait_answer_limit = false;
bool disable_chat = false;
bool wait_answer_speed = false;

//Functions:

void clearEEPROM(){
  displayError("Erasing...");
  delay(1500);
  for (int i = 0; i < EEPROM.length(); i++){
    EEPROM.write(i, 0);
    display.print("erasing 0x");
    display.println(i, HEX);   
    display.display(); 
    delay(10);
  }  
  EEPROM.commit();
  displayError("All memory deleted.");
  delay(2000);
}

bool confirm(){
  disable_chat = true;
  message = "are you sure? (y or n)";
  while (message == "are you sure? (y or n)"){
    ArduinoCloud.update();
  }
  if (message == "y" || message == "Y" || message == "Yes" || message == "yes" || message == "YES"){
    return 1;  
  }
  else if (message == "n" || message == "N" || message == "No" || message == "no" || message == "NO"){
    return 0;
  }
  else{
    message = "invalid. Cancled.";
    ArduinoCloud.update();
    return 0;
  }
}

void onTempatureSetChange()  {
  // Add your code here to act upon TempatureSet change
  if (tempatureSet != 0){
    heating = true;
    awaitUpdate = false;
    display.clearDisplay();
    display.setTextSize(1);
    display.setCursor(0, 8);
    display.print("heating to ");
    display.print(tempatureSet);
    display.print(".");
    display.display();
    delay(3000);
  }
  else{
    heating = false;
    message = "Ready.";
    rewriteLine1(0, "heating turned off.");
    delay(3000);
  }
  ArduinoCloud.update();//update again incase set temperature incramented.
}

//when Time is set
void onSetTimeChange()  {
  // Add your code here to act upon SetTime change
  timeLeft = setTime / 60000 / 60;//show time left in hours.
  if (setTime > 0){
    countDown = setTime * 60000 * 60;//in hours
    countDownTriggered = true;
  }
  else{
    countDownTriggered = false;
    countDownEvent = 0;
    countDown = 0;
  }
  ArduinoCloud.update();//update again incase time incramented.
}

//Heat envirnment
void heatFilament (){
  //if heat is more than the set temp, but less than the overflow:
  if ((heatTempOut >= (tempatureSet + 1)) && (heatTempOut < tempatureSet + overflow)){
    heatIncrement--;
    overflowWarning =false;
    stable = false;
  }
  //is heat is less than what has been set:
  else if (heatTempOut < tempatureSet && heatTempIn <= plate_limit){
    heatIncrement++;
    overflowWarning =false;
    stable = false;
  }
  //if heat is more than the set temp plus 10:
  else if(heatTempOut >= (tempatureSet + overflow) || heatTempIn > plate_limit){
    heatIncrement = 0;
    overflowWarning =true;
    stable = false;
    message = "Warning: Heat Overflow";
    rewriteLine1(8, message);
  }
  //desired heat is reached:
  else{
    stable = true;
  }
  //adjust increment to be within parameter:
  if (heatIncrement > 255){
    heatIncrement = 255;
  }
  if (heatIncrement < 0){
    heatIncrement = 0;
  }

  //set blinkrates:
  if (overflowWarning){
    blinkRate = 100;
    errorBlinkRate = 100;
  }
  else if (stable){
    blinkRate = -1;
    rewriteLine1(8, "Heat is Stable.");
    // analogWrite(heatPin, 0);
  }
  else{
    blinkRate = 10;
    errorBlinkRate = 0;
    rewriteLine1(8, ("heating to " + String(tempatureSet)));
  }

  //Write the increment to pwm pin:
  analogWrite(heatPin, heatIncrement);
  awaitUpdate = false;
  updateTiming = 20000;//update cloud every 20 seconds
}

void updateCloud(){
  if (awaitUpdate == true && (runTime - updateEvent) >= updateTiming){
    if (ArduinoCloud.connected()){
      displayError("Waiting for command..");
      rewriteLine1(56, "updating...");
    }
    else if (!ArduinoCloud.connected()){
      displayError("Wifi not connected.");
    }
    // digitalWrite(statusLed, HIGH);
    // digitalWrite(errorLed, HIGH);
    // Serial.println("Updating...");
    ArduinoCloud.update();
    runTime = millis();
    updateEvent = runTime;
    rewriteLine1(56, message);
  }
  else if ((runTime - updateEvent) >= updateTiming){//updateTiming set to 15 seconds when heating starts
    if (!ArduinoCloud.connected()){
        displayError("Wifi not connected.");
      }
    updateEvent = runTime;
    // Serial.println("Updating...");
    rewriteLine1(56, "updating...");
    ArduinoCloud.update();
    rewriteLine1(56, message);
  }
}
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

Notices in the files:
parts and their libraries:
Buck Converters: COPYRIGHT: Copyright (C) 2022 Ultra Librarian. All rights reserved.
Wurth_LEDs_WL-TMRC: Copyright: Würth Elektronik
